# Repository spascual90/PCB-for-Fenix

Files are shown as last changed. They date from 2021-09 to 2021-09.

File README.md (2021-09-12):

# PCB for Fenix
 PCB to implement Fenix autopilot
 ## Configuration
 ### Fenix PCB v.1.0
 Known errors and limitations
 There is an identified error in the current Fenix PCB design. The pins for PWM/DIR are not correctly allocated. PIN 6&7 are the right PINS. PIN 11&12 should be discarded. In consequence, provisions for these signals in Fenix PCB are not valid.

 Mitigations proposed:
 1 - Usage of a motor controller Arduino shield instead where PWM/DIR pins are directly connected to Arduino through the shield and can be configured correctly to PIN6&7. For this purpose I recommend the shield version of MD10C,
 https://www.robotshop.com/es/es/moto...no-shield.html

 2 - If you already have the MD10C R2 or any other "wired version", and still wants to use Fenix PCB you can still do so, just connect the PWM/DIR pins from motor controller to the arduino 6&7PINS through cables.

 ### Fenix PCB v.1.1-beta.1 patch to fix V1.0 known errors
 WARNING! This patch has not been tested. Use at your own risk.
 - PWM/DIR pins where wrongly allocated to D11, D12. Reallocated to D6, D7.
 - Removed serial I/F expansion: No specific use.
 - J1, J2 screwed plugs shifted. In case of shield pins too short there was a risk of short-circuit with USB plug.
 - Screwed plug pin tags shifted. After screwed plug installation it was not possible to read the text.  

Known errors and limitations
 - Label PWD and DIR are wrongly assigned to connector PINS.
 This issue impacts motor controllers connected to Fenix shield through cables. Not applicable to motor controller Arduino shields.

 Mitigations proposed:
  1 - Swap connector from motor controller PWD to connector DIR in Fenix shield. Swap connector from motor controller DIR to connector PWD in Fenix shield

### Fenix PCB v.1.1-beta.2 patch to fix V1.1-beta.1 known errors
 - PWM/DIR label corrected.
 - Version label added.

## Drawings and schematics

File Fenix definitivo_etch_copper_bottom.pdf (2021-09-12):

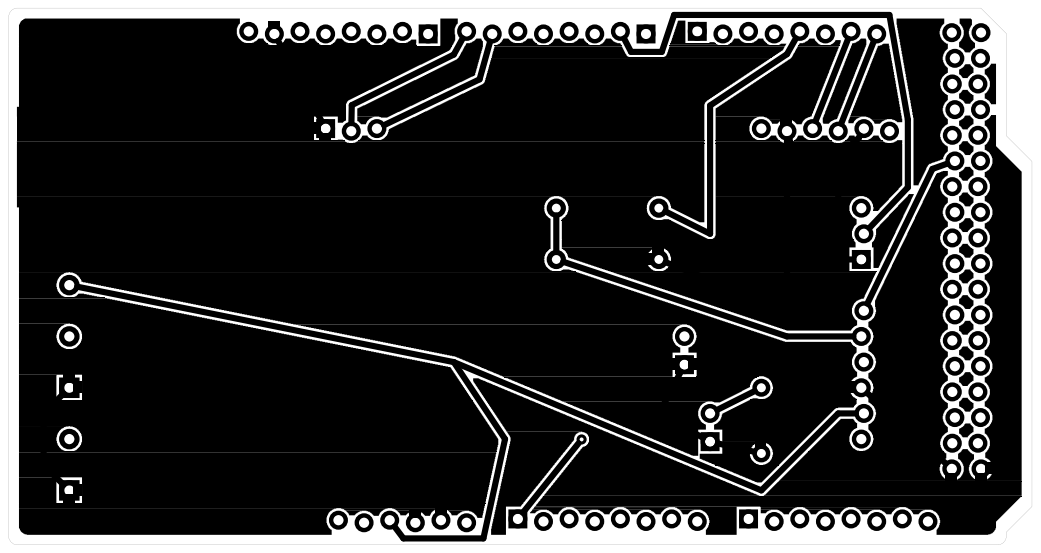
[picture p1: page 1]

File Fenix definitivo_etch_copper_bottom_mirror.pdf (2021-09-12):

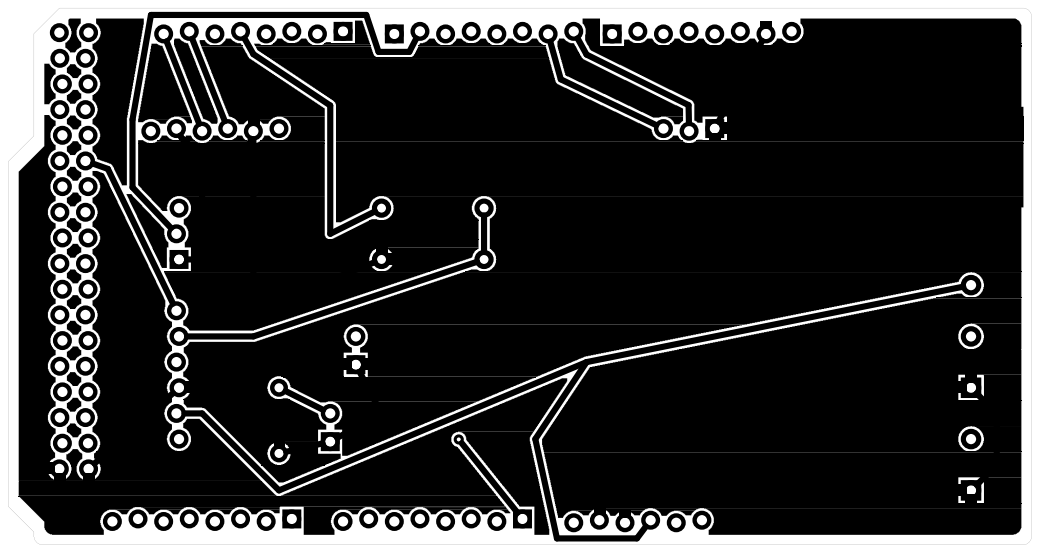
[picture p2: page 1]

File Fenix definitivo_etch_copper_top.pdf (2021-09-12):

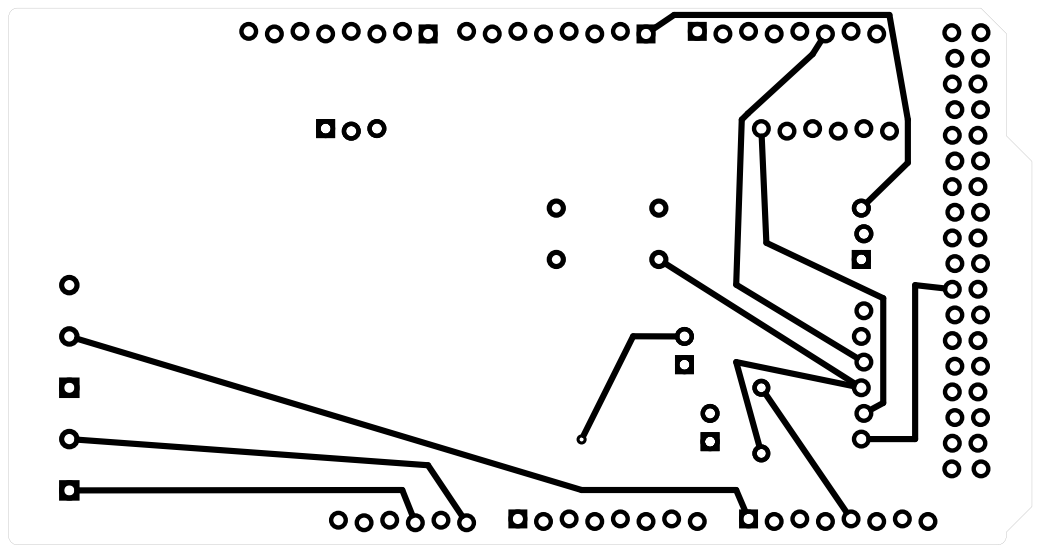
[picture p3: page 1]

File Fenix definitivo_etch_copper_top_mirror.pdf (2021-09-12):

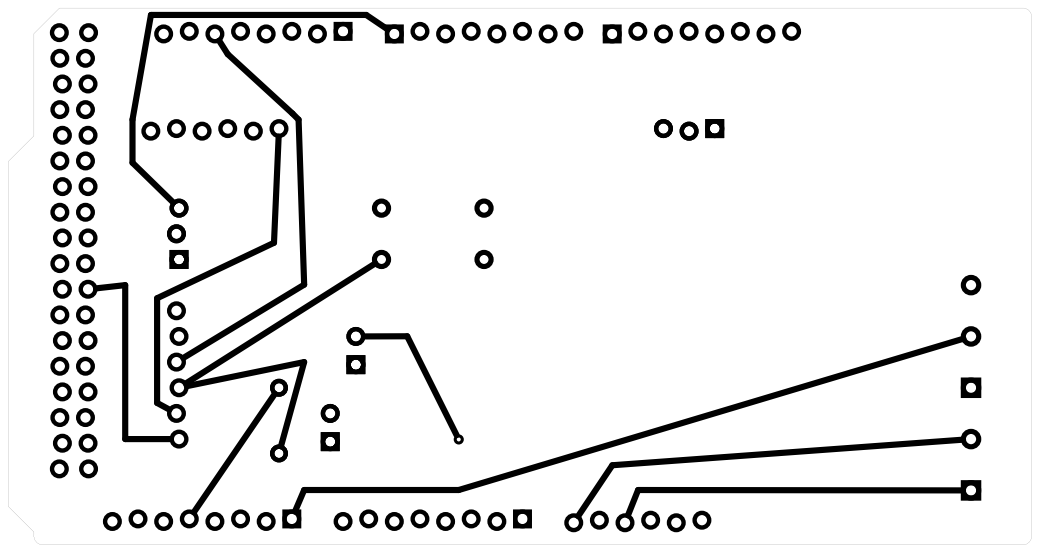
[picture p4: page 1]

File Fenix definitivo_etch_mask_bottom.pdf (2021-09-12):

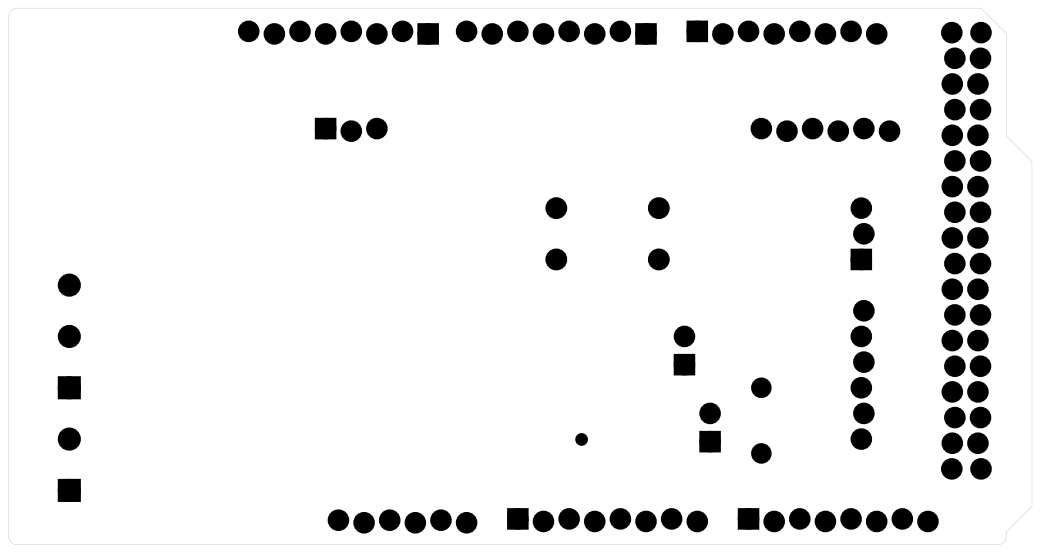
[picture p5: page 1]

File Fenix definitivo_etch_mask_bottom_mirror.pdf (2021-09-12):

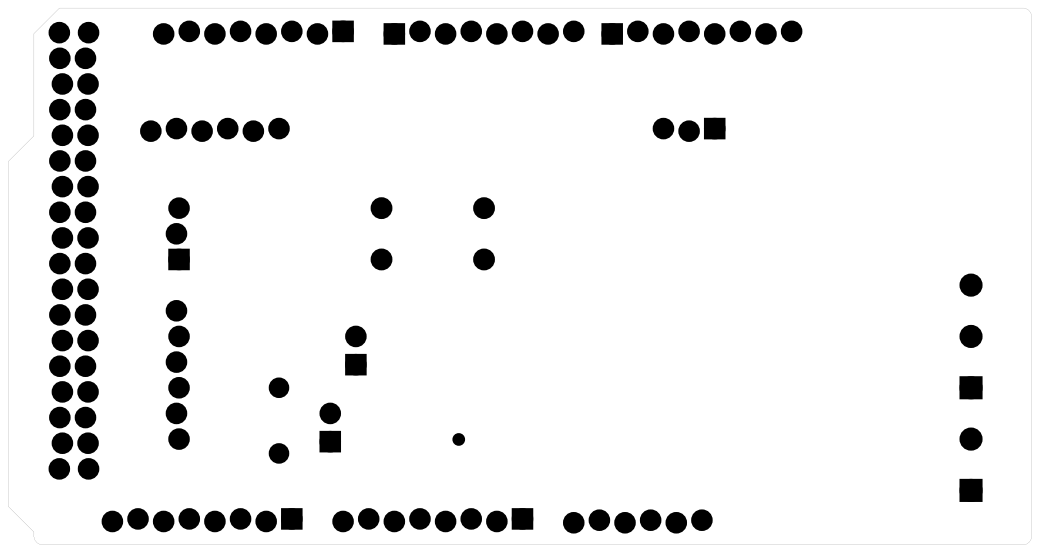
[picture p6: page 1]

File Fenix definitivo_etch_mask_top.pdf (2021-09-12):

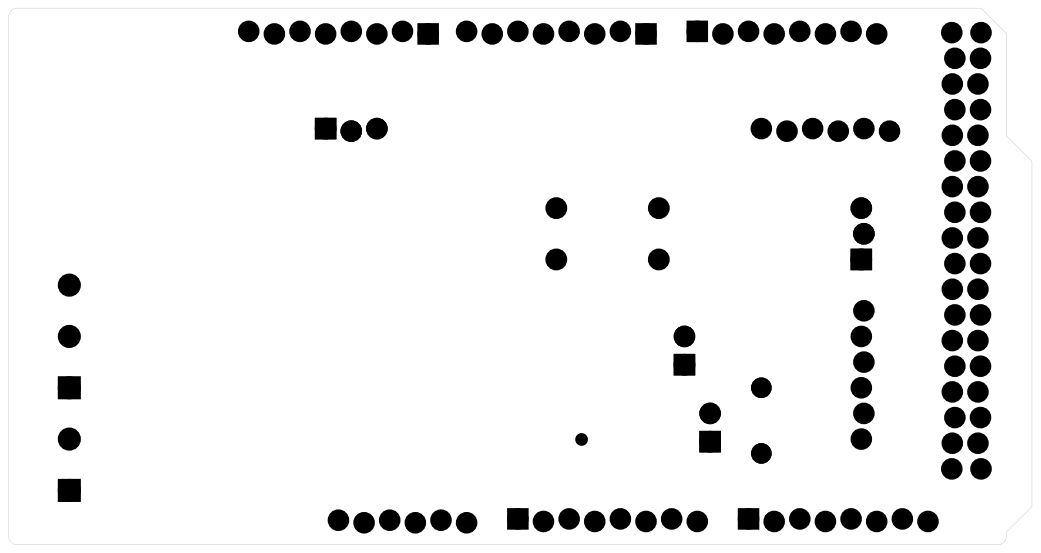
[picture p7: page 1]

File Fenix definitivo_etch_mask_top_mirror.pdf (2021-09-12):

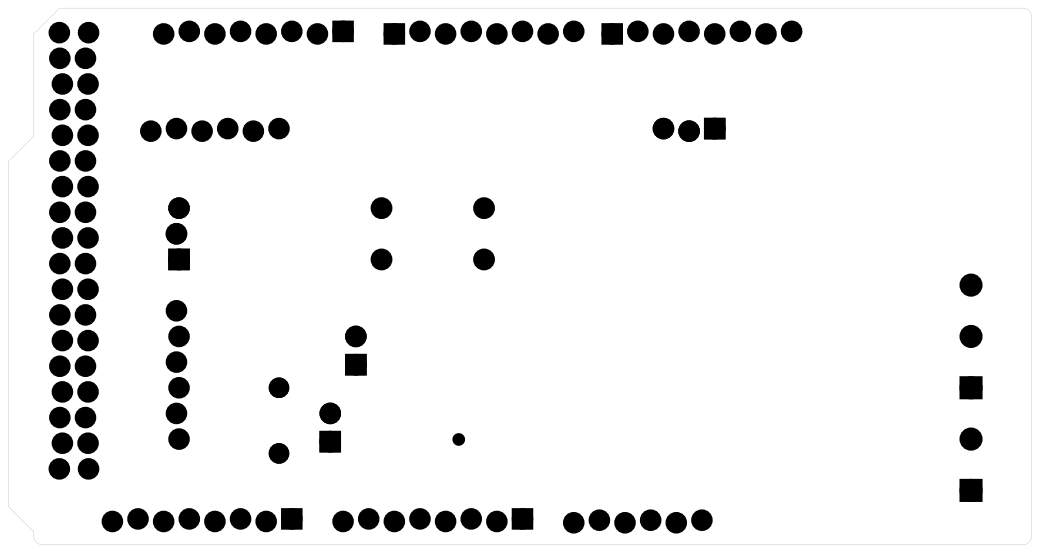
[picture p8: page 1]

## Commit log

2020-03-29 Initial version
    [Fenix PCB completo.fzz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]
2020-06-29 PCB for Fenix v0.2
    [Fenix PCB completo.fzz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]
2020-11-20 Fix of errors
    Check Readme for details
    [Fenix definitivo.fzz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]
2021-09-12 PCB-for-Fenix v1.1-Beta.2
    Check README.md for description of changes
    [Fenix definitivo.fzz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]
